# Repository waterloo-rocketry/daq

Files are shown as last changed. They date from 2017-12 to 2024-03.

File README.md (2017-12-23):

# Waterloo Rocketry Data Acquisition System

Work in progress repo for the next iteration of the WR DAQ. This revision focuses on modularity and extensibility, with the ability to easily add more sensors as required. Schematics of the last revision are in `old/`. The new system supports the following:
* Strain gauges
* 12V pressure transducers
* thermistors/RTDs based on need
* SD card logging using an Arduino
* Logging to an NI DAQ instrumentation module

The system is broken up into boards based on sensor type, with each board managing its own power requirements without the need for a central power board. Sensors can be added by populating more boards (and designing new ones to be added on if necessary). `docs/` will be populated as the project progresses.

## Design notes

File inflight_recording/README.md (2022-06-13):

# HOW TO SETUP IN-FLIGHT RECORDING USING A RASPBERRY PI ZERO W

## Instructions

### Basic Pi setup

1. Flash a default copy of the Raspbian OS onto a large-capacity SD card (pereferably 128 GB or larger)
1. [Enable SSH](https://www.raspberrypi.org/documentation/remote-access/ssh/README.md) (skip to step 3 - `Enable SSH on a headless Raspberry Pi`)
1. Follow the `Direct USB Connection (Pi Zero / Zero W Only)` section of [this article](https://www.tomshardware.com/reviews/raspberry-pi-headless-setup-how-to,6028.html)
1. Plug the camera module into the Pi using a ribbon cable
1. Use a USB Micro B cable to connect the Pi to a computer (ensure you are connecting to the 'USB' port, not the 'PWR' port)
1. SSH into the Pi (using PuTTY, or similar):
    1. host/ip: raspberrypi.local if USB connected OR the IP of the Pi (see [Getting the IP of the Pi](#getting-the-ip-of-the-pi) for help)
    1. user: pi
    1. password: raspberry
    1. port: 22
1. Inside the ssh session, [enable the camera](https://www.raspberrypi.org/documentation/configuration/camera.md) and [connect the Pi to the Internet](https://www.raspberrypi.org/documentation/configuration/wireless/wireless-cli.md)
1. Update the [Raspbian OS](https://www.raspberrypi.org/documentation/raspbian/updating.md) (Internet connection required)

### Setting up the picam

1. Establish an FTP connection (or however you want to transfer files) to the Pi (see [Transferring files to and from the Pi](#transferring-files-to-and-from-the-pi) for help)
1. In the `home/Documents` folder, make a folder called `picam`
1. Download all files in this directory onto your computer (do not transfer them yet)
1. **Convert ALL line endings in the `.sh` and `.service` files to UNIX-style line endings (LF)**
    1. Skipping this step will result in the service NOT running.
    1. In Notepad++, this can be done by opening the file -> edit -> EOL conversion -> UNIX (LF)
1. Transfer the converted files into `picam` on the raspberry pi (see [Transferring files to and from the Pi](#transferring-files-to-and-from-the-pi) for help)
1. SSH into the Pi
1. Run `cd picam` to move into the correct directory
1. Run `chmod u+x picam_setup.sh`
1. Run `./picam_setup.sh` to configure the picam service

Done! Next time the Pi restarts, the camera will run and will stream its data over the network.

### Streaming footage

1. Download [mpv](https://mpv.io/), a media player (does not require installation, it's a portable software)
1. Extract the contents of the zip to a file, and open a command prompt to that location
1. Ensure the Pi is turned on, and give it a minute to start up fully
1. Run `mpv.exe --no-cache --untimed --no-demuxer-thread udp://<IPv4 Address of Your PC>:<PORT>` (see [Getting the IP of your PC](#getting-the-ip-of-your-pc) for help)
    1. The port and IP are the ones you specified in `picam_setup.sh`. If you don't know it, you'll have to check what is currently on the Pi.

Done! The stream should appear. If there is significant delay, try restarting the stream. Generally, about ~1 second of delay is expected. If no footage appears, check your firewall settings and ensure the port(s) allow UDP traffic.

## Additional Info

### Getting the IP of the Pi

1. If you are able to connect to the Pi via USB:
    1. SSH into the Pi (see [Basic Pi setup](#basic-pi-setup))
    1. Run `ifconfig`
    1. Under `wlan0`, the copy and record the address next to `inet` (usually something like 192.168.x.xx)
1. If you do not have access to the Pi:
    1. Login to your WiFi network's remote gateway (this is usually only possible if you are the administrator of your wifi network)
    1. Find the active devices list
    1. Copy the IP Address of the Raspberry Pi on the network.

If you do not have physical access AND you are not the administrator of the WiFi network, there is no way to get this address unfortunately.

### Getting the IP of your PC

These are Windows instructions. If you have Linux, you already know how to do this. If you have a mac, MPV doesn't work on it anyway.

1. Ensure you are connected to the same network as the Pi
1. Open a command prompt
1. Run `ipconfig`
1. Scroll to `Wireless LAN adapter Wi-Fi` (if you're on ethernet, it'll be `Ethernet adapter Ethernet`)
1. Find your `IPv4` address. This is your local IP.

Similar to above in [Getting the IP of the Pi](#getting-the-ip-of-the-pi), if you have access to the network's remote gateway, you can find your PC in the active devices list (works on any device)

### Transferring files to and from the Pi

There are many ways to accomplish this but an easy, free way to do this is using FileZilla, an FTP client.

1. Download and install [FileZilla](https://filezilla-project.org/)
1. Input the following details in the top-bar to establish a connection to the Pi
    1. host/ip: raspberrypi.local if USB connected OR the IP of the Pi (see [Getting the IP of the Pi](#getting-the-ip-of-the-pi) for help)
    1. user: pi
    1. password: raspberry
    1. port: 22
1. Click `quickconnect`
1. The `/home/pi` folder should appear in the `remote site` tab
1. PiCam files are stored in the `picam` directory.
1. To upload files, simply navigate to the folder containing the desired file(s) on the `local site`, select them, right click -> upload
1. To download files, simply navigate to the folder containing the desired file(s) on the `remote site`, select them, right click -> download

### Tips if you're running into issues

If lagging occurs, it may be possible that the `gpu_mem` component of `/boot/config.txt` needs to be upped to 256. We upped it on the prototype, but did not test if it was required

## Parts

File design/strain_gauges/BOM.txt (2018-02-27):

Strain Gauge Board BOM

Part Name, Digikey Number
LT-1460, LT1460GIZ-10#PBF-ND
TL780-15, 296-14326-5-ND
INA126, INA126PA-ND
2 Pin Conn, 609-4725-ND
3 Pin Conn, 277-1722-ND
4 Pin Conn, 277-1860-ND

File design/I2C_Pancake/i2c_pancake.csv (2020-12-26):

Source: | C:\Users\zacha\Desktop\Zachary\Rocketry\daq\daq\design\I2C Pancake\i2c_pancake.sch
Date: | 30-Sep-2020 16:33:39
Tool: | Eeschema (5.1.4)-1
Generator: | C:\Program Files\KiCad\bin\scripting\plugins/bom_csv_grouped_by_value.py
Component Count: | 39
Individual Components:
Item | Qty | Reference(s) | Value | LibPart | Footprint | Datasheet
 |  | C1 | 0.1 uF | Device:C | footprints:C_0805_HandSoldering | ~
 |  | C2 | 10 uF | Device:C | footprints:C_0805_HandSoldering | ~
 |  | C3 | 0.1uF | Device:C | footprints:C_0805_HandSoldering | ~
 |  | C4 | 0.1uF | i2c_pancake-rescue:C-device-i2c_pancake-rescue | footprints:C_0805_HandSoldering
 |  | C5 | 0.1uF | i2c_pancake-rescue:C-device-i2c_pancake-rescue | footprints:C_0805_HandSoldering
 |  | C6 | 0.1uF | i2c_pancake-rescue:C-device-i2c_pancake-rescue | footprints:C_0805_HandSoldering
 |  | D1 | LED | Device:LED | LED_SMD:LED_1206_3216Metric_Pad1.42x1.75mm_HandSolder | ~
 |  | D2 | DDZ4V7ASF-7 | Device:D_Zener_ALT | Diode_SMD:D_SOD-323F | ~
 |  | D3 | DDZ4V7ASF-7 | Device:D_Zener_ALT | Diode_SMD:D_SOD-323F | ~
 |  | D4 | DDZ4V7ASF-7 | Device:D_Zener_ALT | Diode_SMD:D_SOD-323F | ~
 |  | F1 | Fuse | i2c_pancake-rescue:Fuse-device-i2c_pancake-rescue | Fuse:Fuse_0805_2012Metric_Pad1.15x1.40mm_HandSolder
 |  | J1 | Conn_01x05_Male | Connector:Conn_01x05_Male | Connector_JST:JST_XH_S5B-XH-A-1_1x05_P2.50mm_Horizontal | ~
 |  | J2 | Conn_01x05_Male | Connector:Conn_01x05_Male | Connector_JST:JST_XH_S5B-XH-A-1_1x05_P2.50mm_Horizontal | ~
 |  | J3 | Conn_01x03 | i2c_pancake-rescue:Conn_01x03-strain_gauges_rtr-rescue-i2c_pancake-rescue | TerminalBlock_Phoenix:TerminalBlock_Phoenix_MKDS-1,5-3_1x03_P5.00mm_Horizontal
 |  | J4 | Conn_01x03 | i2c_pancake-rescue:Conn_01x03-strain_gauges_rtr-rescue-i2c_pancake-rescue | TerminalBlock_Phoenix:TerminalBlock_Phoenix_MKDS-1,5-3_1x03_P5.00mm_Horizontal
 |  | J5 | Conn_01x05_Female | Connector:Conn_01x05_Female | footprints:PinHeader_5x2.54_SMD_90deg_952-3198-1-ND | ~
 |  | J6 | Conn_01x04 | i2c_pancake-rescue:Conn_01x04-strain_gauges_rtr-rescue-i2c_pancake-rescue | TerminalBlock_Phoenix:TerminalBlock_Phoenix_MKDS-1,5-4_1x04_P5.00mm_Horizontal
 |  | J7 | Conn_01x04 | i2c_pancake-rescue:Conn_01x04-strain_gauges_rtr-rescue-i2c_pancake-rescue | TerminalBlock_Phoenix:TerminalBlock_Phoenix_MKDS-1,5-4_1x04_P5.00mm_Horizontal
 |  | J8 | Conn_01x04 | i2c_pancake-rescue:Conn_01x04-strain_gauges_rtr-rescue-i2c_pancake-rescue | TerminalBlock_Phoenix:TerminalBlock_Phoenix_MKDS-1,5-4_1x04_P5.00mm_Horizontal
 |  | R1 | 10K | Device:R | footprints:R_0805_HandSoldering | ~
 |  | R2 | 10K | i2c_pancake-rescue:R-device-i2c_pancake-rescue | footprints:R_0805_HandSoldering
 |  | R3 | 5K | i2c_pancake-rescue:R-device-i2c_pancake-rescue | footprints:R_0805_HandSoldering
 |  | R4 | 330 | Device:R | footprints:R_0805_HandSoldering | ~
 |  | R5 | 10K | Device:R | footprints:R_0805_HandSoldering | ~
 |  | R6 | 10K | Device:R | footprints:R_0805_HandSoldering | ~
 |  | R7 | 10K | Device:R | footprints:R_0805_HandSoldering | ~
 |  | R8 | 10K | Device:R | footprints:R_0805_HandSoldering | ~
 |  | R9 | R | i2c_pancake-rescue:R-device-i2c_pancake-rescue | footprints:R_0805_HandSoldering
 |  | R10 | 0 | i2c_pancake-rescue:R-device-i2c_pancake-rescue | footprints:R_0805_HandSoldering
 |  | R11 | R | i2c_pancake-rescue:R-device-i2c_pancake-rescue | footprints:R_0805_HandSoldering
 |  | R12 | 0 | i2c_pancake-rescue:R-device-i2c_pancake-rescue | footprints:R_0805_HandSoldering
 |  | R13 | R | i2c_pancake-rescue:R-device-i2c_pancake-rescue | footprints:R_0805_HandSoldering
 |  | R14 | 0 | i2c_pancake-rescue:R-device-i2c_pancake-rescue | footprints:R_0805_HandSoldering
 |  | SW1 | SW_DIP_x04 | Switch:SW_DIP_x04 | footprints:DIP_SWITCH_4X2 | ~
 |  | U1 | TL750M10CKVU | tlv750m10:TL750M05CKVURG3 | footprints:TL750M10CKVU | http://www.ti.com/lit/ds/symlink/tl750m.pdf?ts=1588185394744
 |  | U2 | PIC16F1826-ISO | i2c_pancake-rescue:PIC16F1826-ISO-rlcsv3_modular-rescue | custom:PIC16F1826-ISO
 |  | U3 | INA826 | i2c_pancake-rescue:INA826-daq_components-i2c_pancake-rescue | footprints:SOIC-8_3.9x4.9mm_Pitch1.27mm_HandSoldering
 |  | U4 | INA826 | i2c_pancake-rescue:INA826-daq_components-i2c_pancake-rescue | footprints:SOIC-8_3.9x4.9mm_Pitch1.27mm_HandSoldering
 |  | U5 | INA826 | i2c_pancake-rescue:INA826-daq_components-i2c_pancake-rescue | footprints:SOIC-8_3.9x4.9mm_Pitch1.27mm_HandSoldering
Collated Components:
Item | Qty | Reference(s) | Value | LibPart | Footprint | Datasheet
1 | 1 | C1 | 0.1 uF | Device:C | footprints:C_0805_HandSoldering | ~
2 | 1 | C2 | 10 uF | Device:C | footprints:C_0805_HandSoldering | ~
3 | 1 | C3 | 0.1uF | Device:C | footprints:C_0805_HandSoldering | ~
4 | 3 | C4, C5, C6 | 0.1uF | i2c_pancake-rescue:C-device-i2c_pancake-rescue | footprints:C_0805_HandSoldering
5 | 1 | D1 | LED | Device:LED | LED_SMD:LED_1206_3216Metric_Pad1.42x1.75mm_HandSolder | ~
6 | 3 | D2, D3, D4 | DDZ4V7ASF-7 | Device:D_Zener_ALT | Diode_SMD:D_SOD-323F | ~
7 | 1 | F1 | Fuse | i2c_pancake-rescue:Fuse-device-i2c_pancake-rescue | Fuse:Fuse_0805_2012Metric_Pad1.15x1.40mm_HandSolder
8 | 2 | J1, J2 | Conn_01x05_Male | Connector:Conn_01x05_Male | Connector_JST:JST_XH_S5B-XH-A-1_1x05_P2.50mm_Horizontal | ~
9 | 2 | J3, J4 | Conn_01x03 | i2c_pancake-rescue:Conn_01x03-strain_gauges_rtr-rescue-i2c_pancake-rescue | TerminalBlock_Phoenix:TerminalBlock_Phoenix_MKDS-1,5-3_1x03_P5.00mm_Horizontal
10 | 1 | J5 | Conn_01x05_Female | Connector:Conn_01x05_Female | footprints:PinHeader_5x2.54_SMD_90deg_952-3198-1-ND | ~
11 | 3 | J6, J7, J8 | Conn_01x04 | i2c_pancake-rescue:Conn_01x04-strain_gauges_rtr-rescue-i2c_pancake-rescue | TerminalBlock_Phoenix:TerminalBlock_Phoenix_MKDS-1,5-4_1x04_P5.00mm_Horizontal
12 | 5 | R1, R5, R6, R7, R8 | 10K | Device:R | footprints:R_0805_HandSoldering | ~
13 | 1 | R2 | 10K | i2c_pancake-rescue:R-device-i2c_pancake-rescue | footprints:R_0805_HandSoldering
14 | 1 | R3 | 5K | i2c_pancake-rescue:R-device-i2c_pancake-rescue | footprints:R_0805_HandSoldering
15 | 1 | R4 | 330 | Device:R | footprints:R_0805_HandSoldering | ~
16 | 3 | R9, R11, R13 | R | i2c_pancake-rescue:R-device-i2c_pancake-rescue | footprints:R_0805_HandSoldering
17 | 3 | R10, R12, R14 | 0 | i2c_pancake-rescue:R-device-i2c_pancake-rescue | footprints:R_0805_HandSoldering
18 | 1 | SW1 | SW_DIP_x04 | Switch:SW_DIP_x04 | footprints:DIP_SWITCH_4X2 | ~
19 | 1 | U1 | TL750M10CKVU | tlv750m10:TL750M05CKVURG3 | footprints:TL750M10CKVU | http://www.ti.com/lit/ds/symlink/tl750m.pdf?ts=1588185394744
20 | 1 | U2 | PIC16F1826-ISO | i2c_pancake-rescue:PIC16F1826-ISO-rlcsv3_modular-rescue | custom:PIC16F1826-ISO
21 | 3 | U3, U4, U5 | INA826 | i2c_pancake-rescue:INA826-daq_components-i2c_pancake-rescue | footprints:SOIC-8_3.9x4.9mm_Pitch1.27mm_HandSoldering

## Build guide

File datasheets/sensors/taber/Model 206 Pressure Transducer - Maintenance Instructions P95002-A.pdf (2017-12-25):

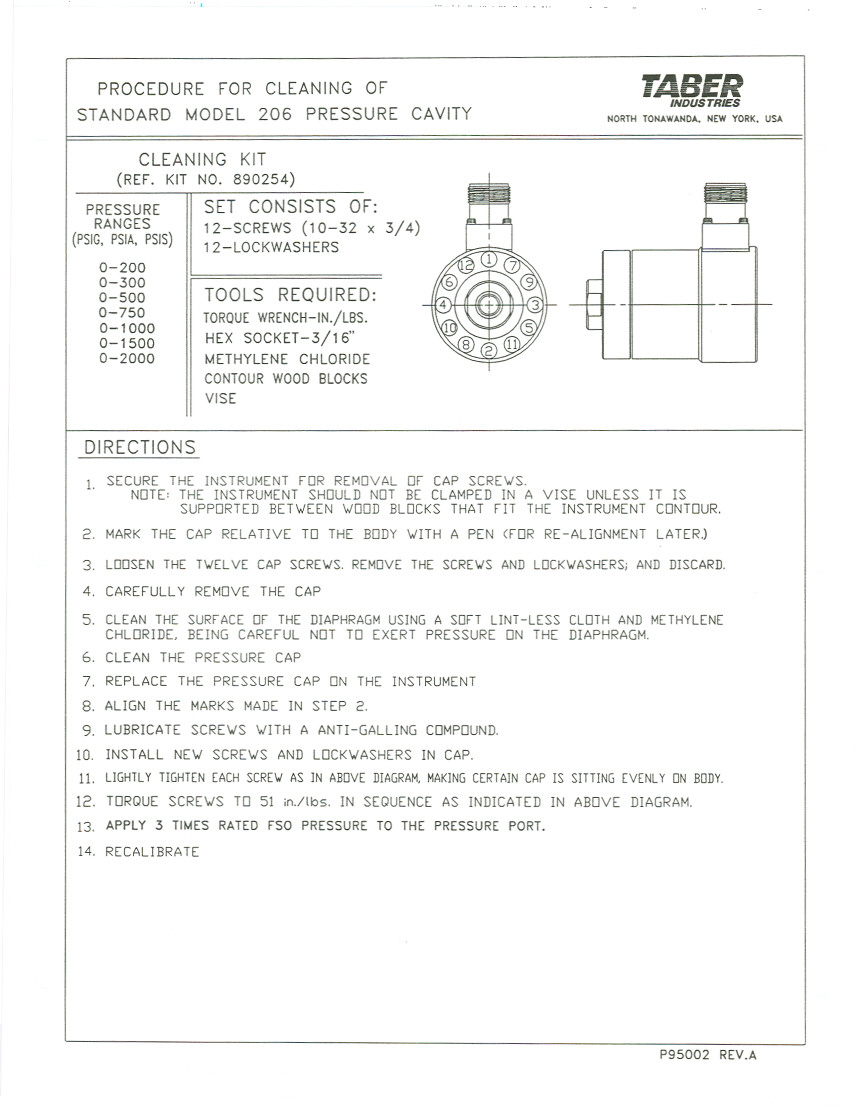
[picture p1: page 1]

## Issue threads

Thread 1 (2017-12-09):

Temperature measurement boards

amihaila, 2017-12-09:
Either thermistors or RTDs, depending on use case. Thermistors are enough if we don't want to measure any high temperatures.

Closed 2020-10-06.

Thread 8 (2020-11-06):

Schematic for Strain gauge rtr is out of date

ewdyang, 2020-11-06:
The 15V regulator in the schematics has been changed to a 12V version (TL780-12KCS)

BluCodeGH, 2022-11-04:
Closing as no longer relevant

Closed 2022-11-04.

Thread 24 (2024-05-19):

Thermocouple board issues

JasonBrave, 2024-05-19:
1. Screw terminals are not labeled

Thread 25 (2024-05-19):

Patch Panel Board Issue

JasonBrave, 2024-05-19:
12 pin terminal is in wrong direction

Pdada1, 2024-05-21:
Silkscreen Issues
-No silkscreen on power jumpers (unknown which pin is which voltage)
-Same with the big terminal block (weidmuller)

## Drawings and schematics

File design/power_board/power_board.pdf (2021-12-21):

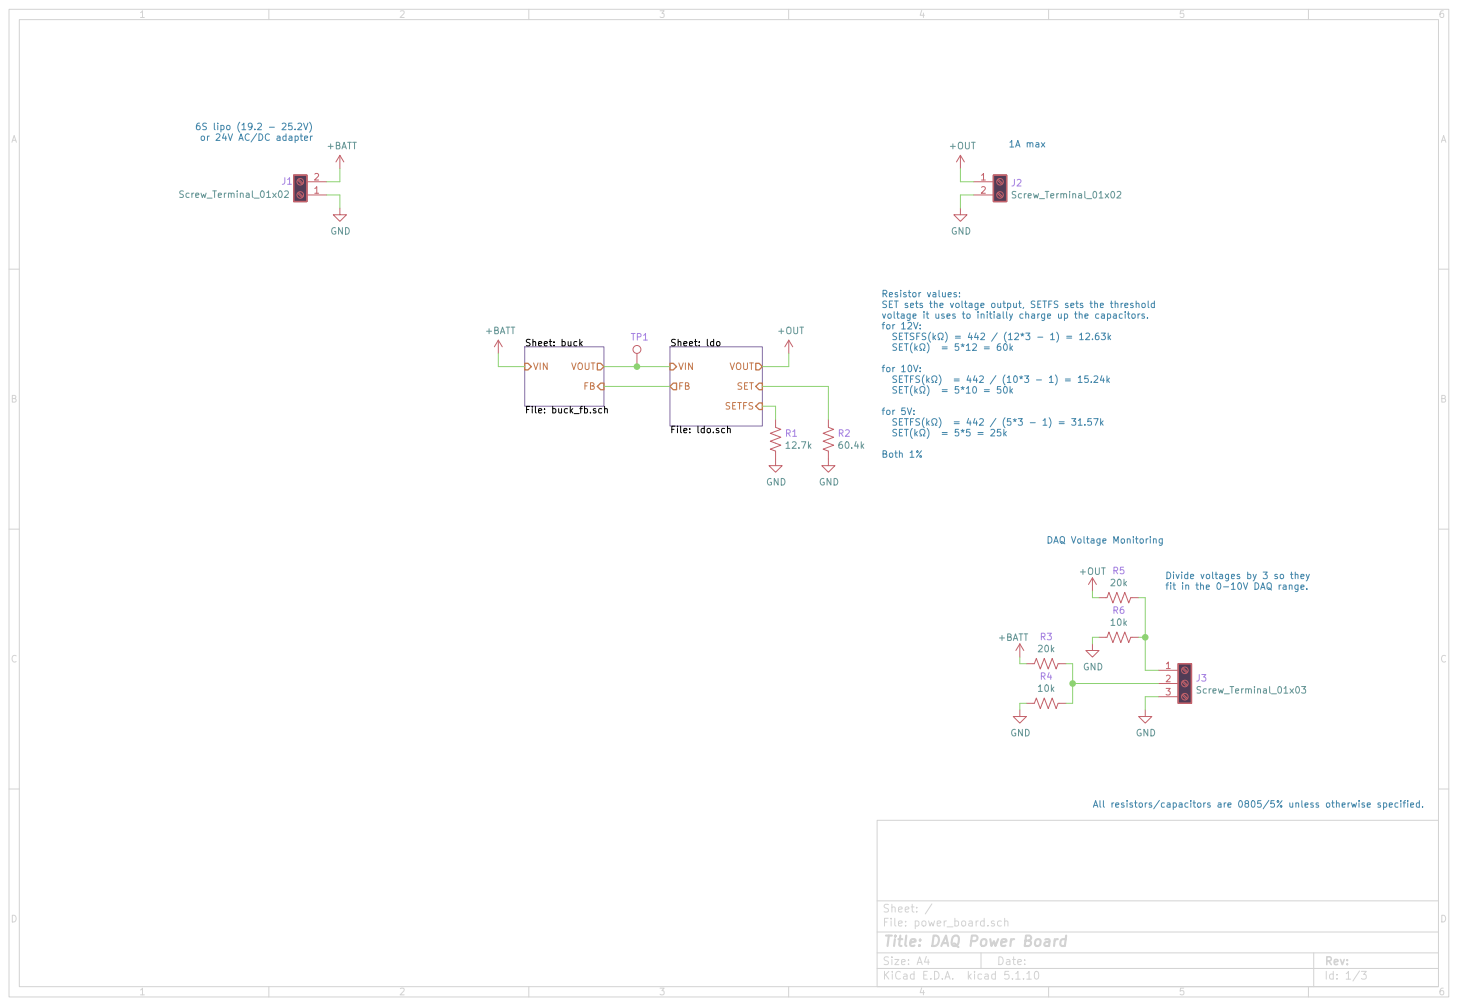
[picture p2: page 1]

6S lipo (19.2 - 25.2V)
or 24V AC/DC adapter

DAQ Voltage Monitoring Resistor values: SET sets the voltage output, SETFS sets the threshold

voltage it uses to initially charge up the capacitors.
for 12V:
SETSFS(k) = 442 / (12*3 - 1) = 12.63k
SET(k) = 5*12 = 60k

Sheet: ldo File: ldo.sch VIN

Divide voltages by 3 so they
fit in the 0-10V DAQ range.

All resistors/capacitors are 0805/5% unless otherwise specified.

File: power_board.sch Sheet: /
Id: 1/3 Title: DAQ Power Board

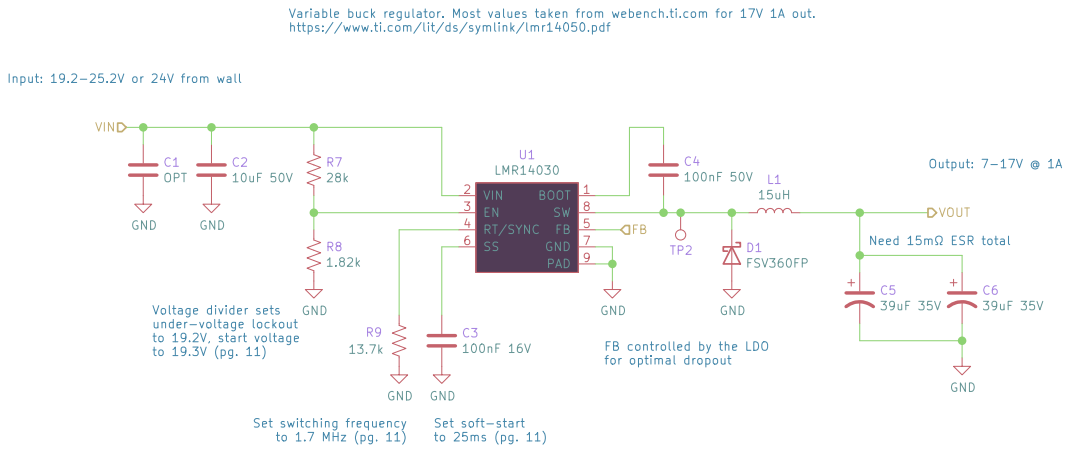
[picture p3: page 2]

Variable buck regulator. Most values taken from webench.ti.com for 17V 1A out.
https://www.ti.com/lit/ds/symlink/lmr14050.pdf

Input: 19.2-25.2V or 24V from wall

Output: 7-17V @ 1A Need 15m ESR total Voltage divider sets

for optimal dropout Set soft-start

FB controlled by the LDO

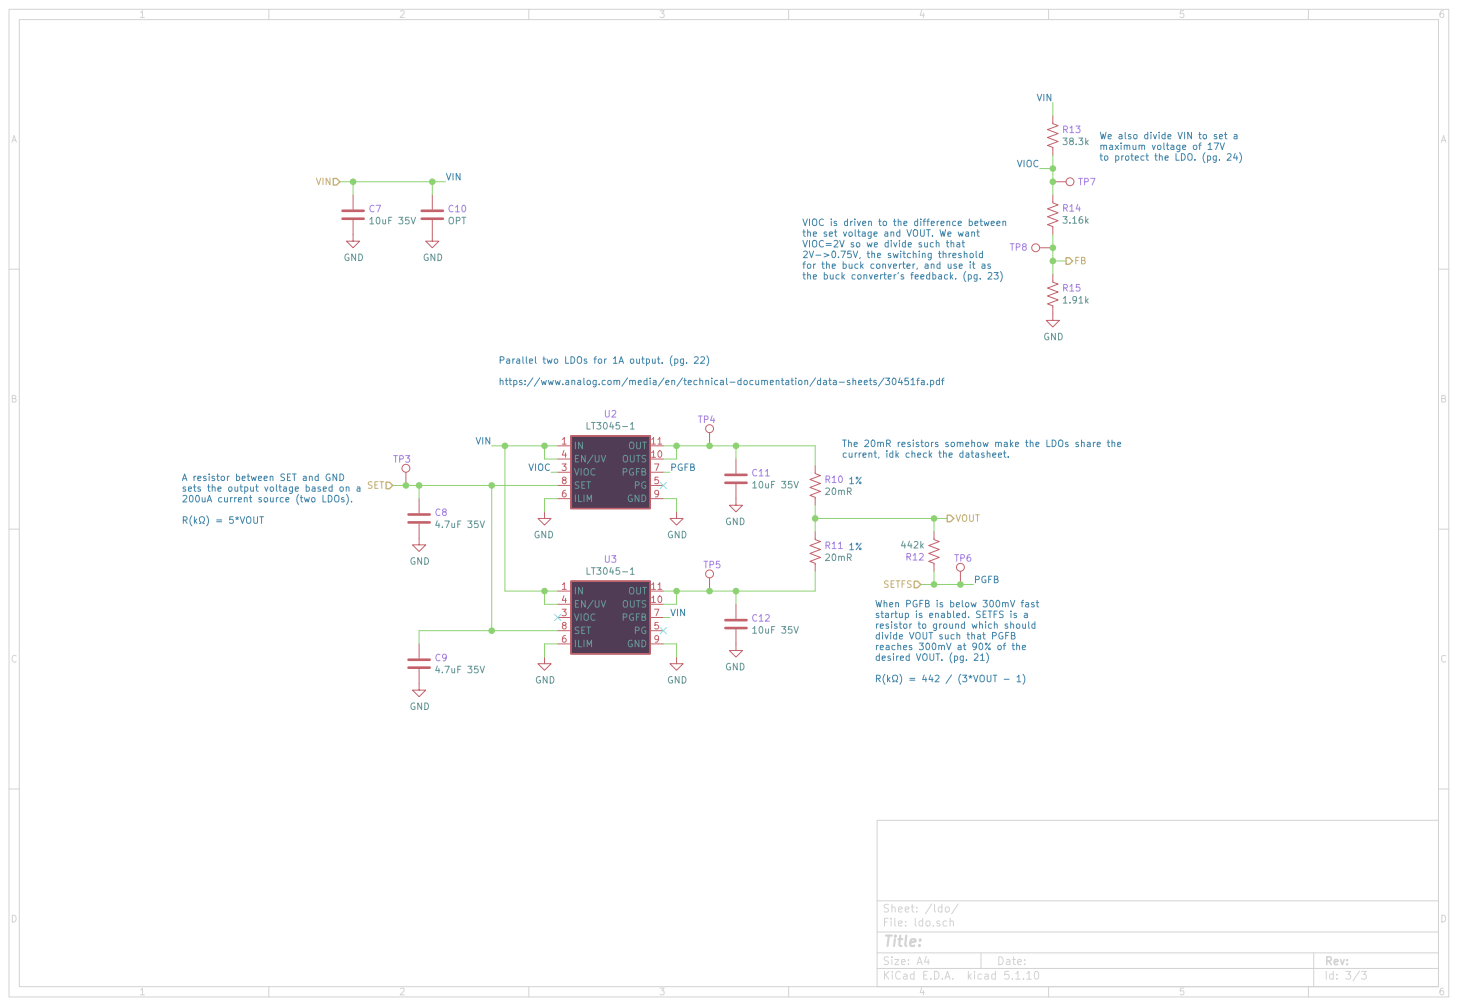
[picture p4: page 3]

to protect the LDO. (pg. 24) 1%

VIOC is driven to the difference between
the set voltage and VOUT. We want VIOC=2V so we divide such that 2V->0.75V, the switching threshold

for the buck converter, and use it as

current, idk check the datasheet. Parallel two LDOs for 1A output. (pg. 22)

https://www.analog.com/media/en/technical-documentation/data-sheets/30451fa.pdf A resistor between SET and GND

The 20mR resistors somehow make the LDOs share the

sets the output voltage based on a
200uA current source (two LDOs).

resistor to ground which should
divide VOUT such that PGFB
reaches 300mV at 90% of the
desired VOUT. (pg. 21)

Id: 3/3 Title: File: ldo.sch Sheet: /ldo/

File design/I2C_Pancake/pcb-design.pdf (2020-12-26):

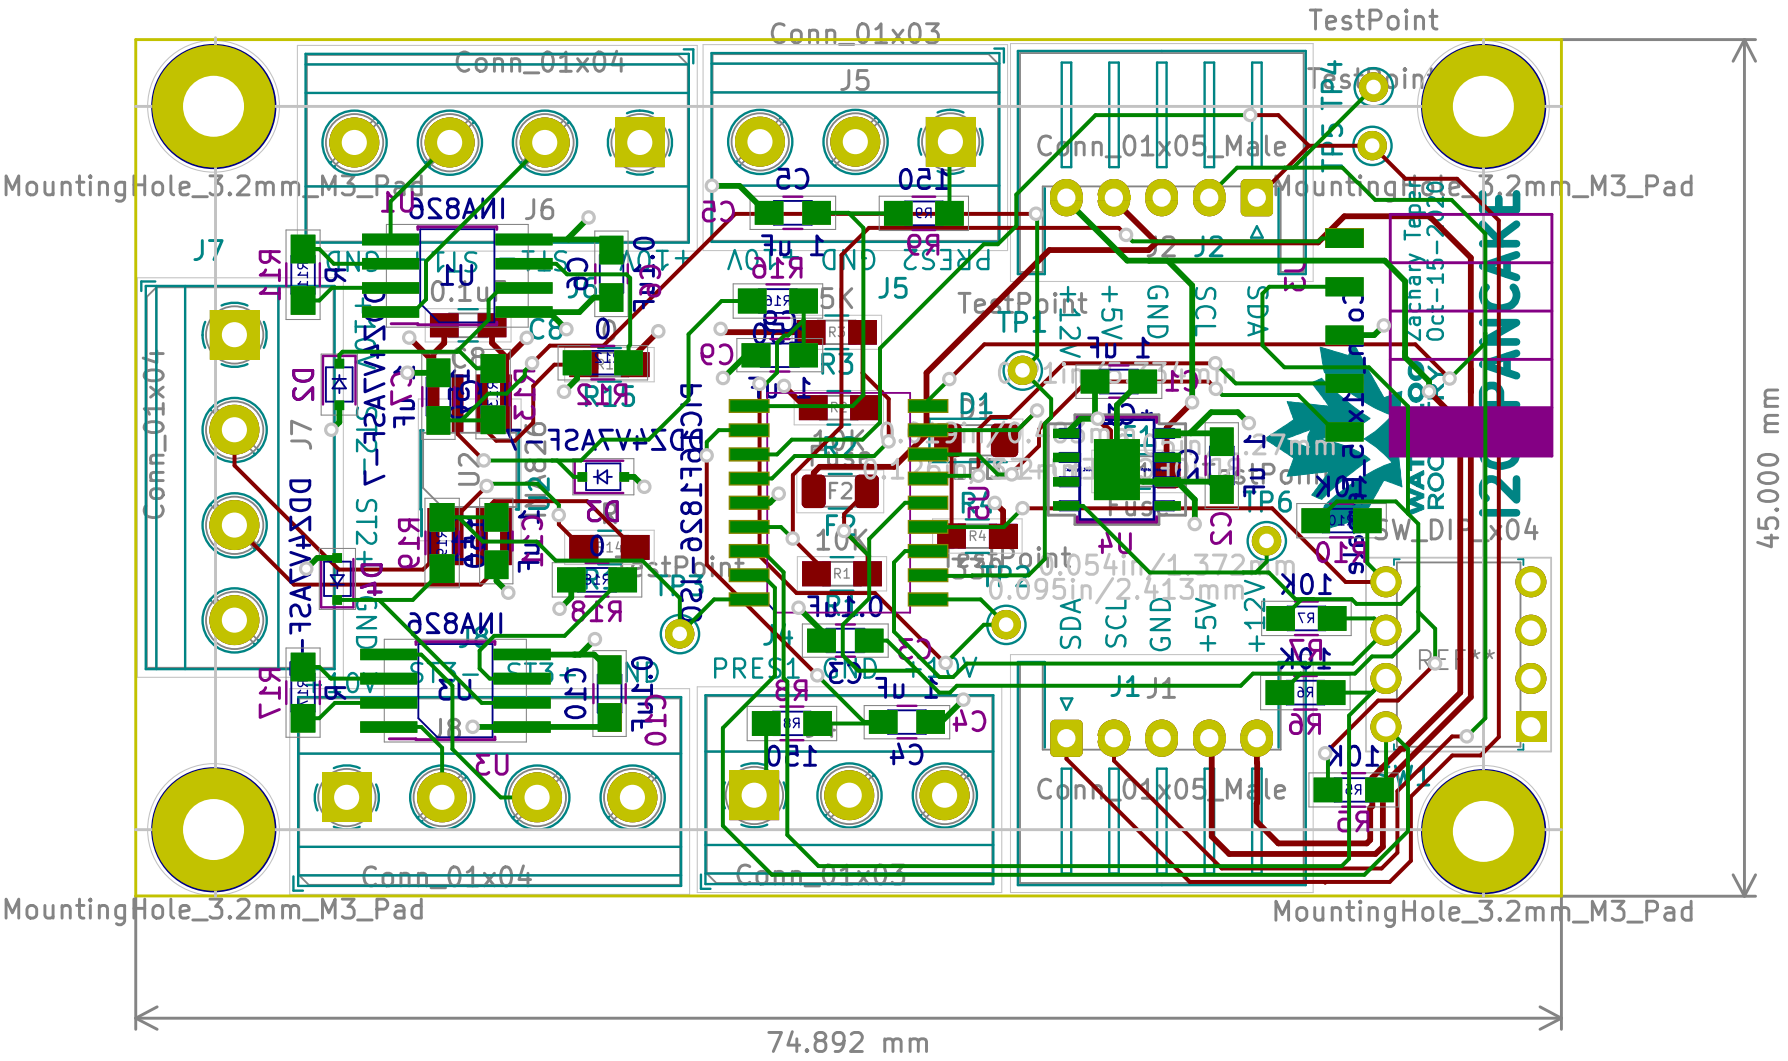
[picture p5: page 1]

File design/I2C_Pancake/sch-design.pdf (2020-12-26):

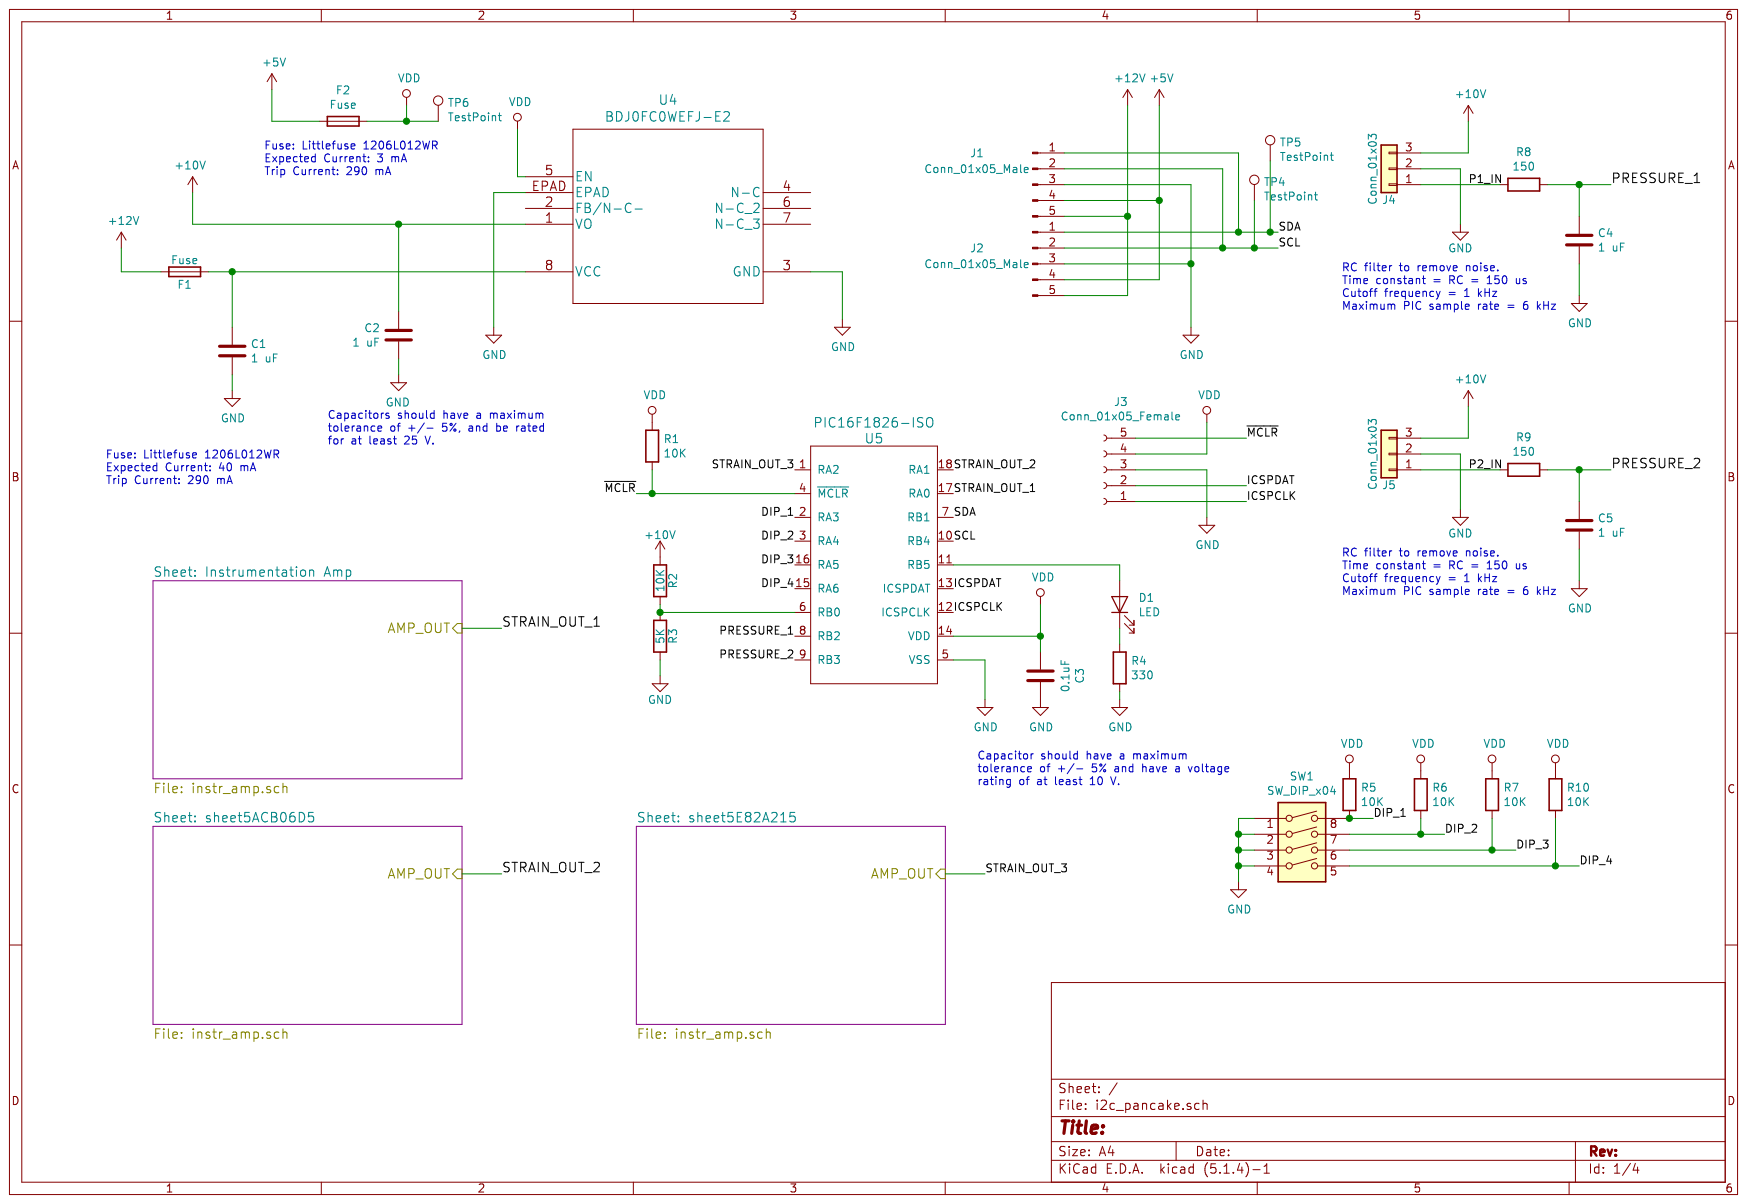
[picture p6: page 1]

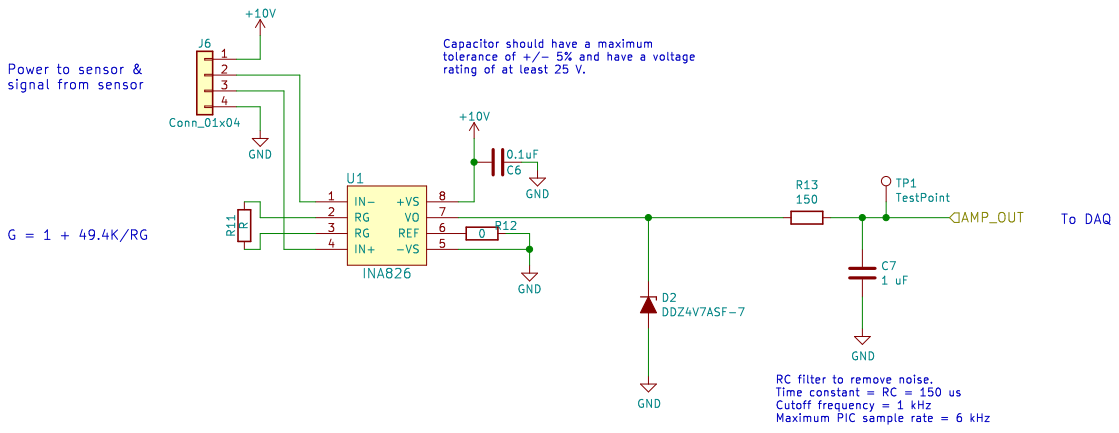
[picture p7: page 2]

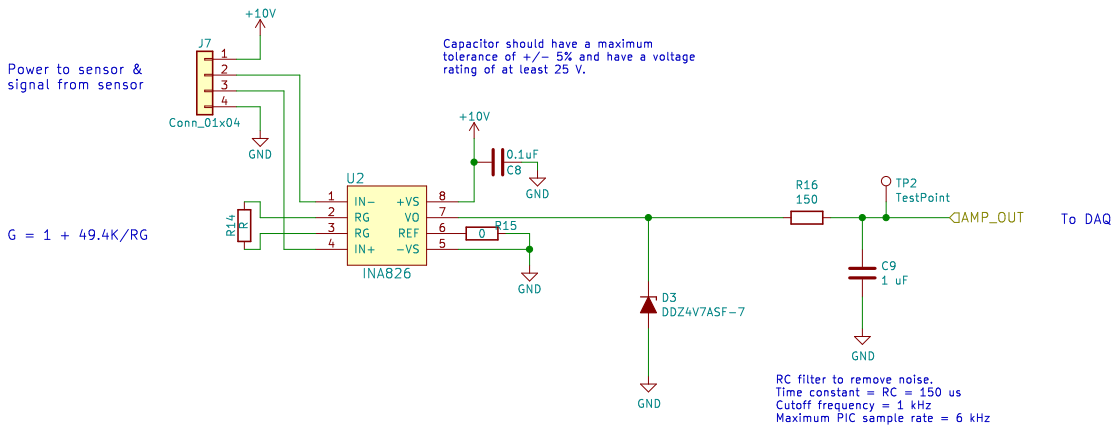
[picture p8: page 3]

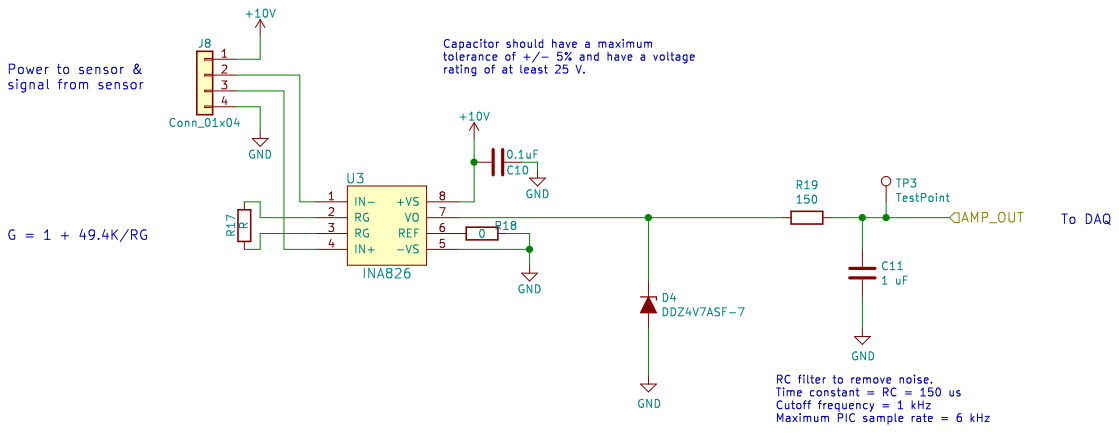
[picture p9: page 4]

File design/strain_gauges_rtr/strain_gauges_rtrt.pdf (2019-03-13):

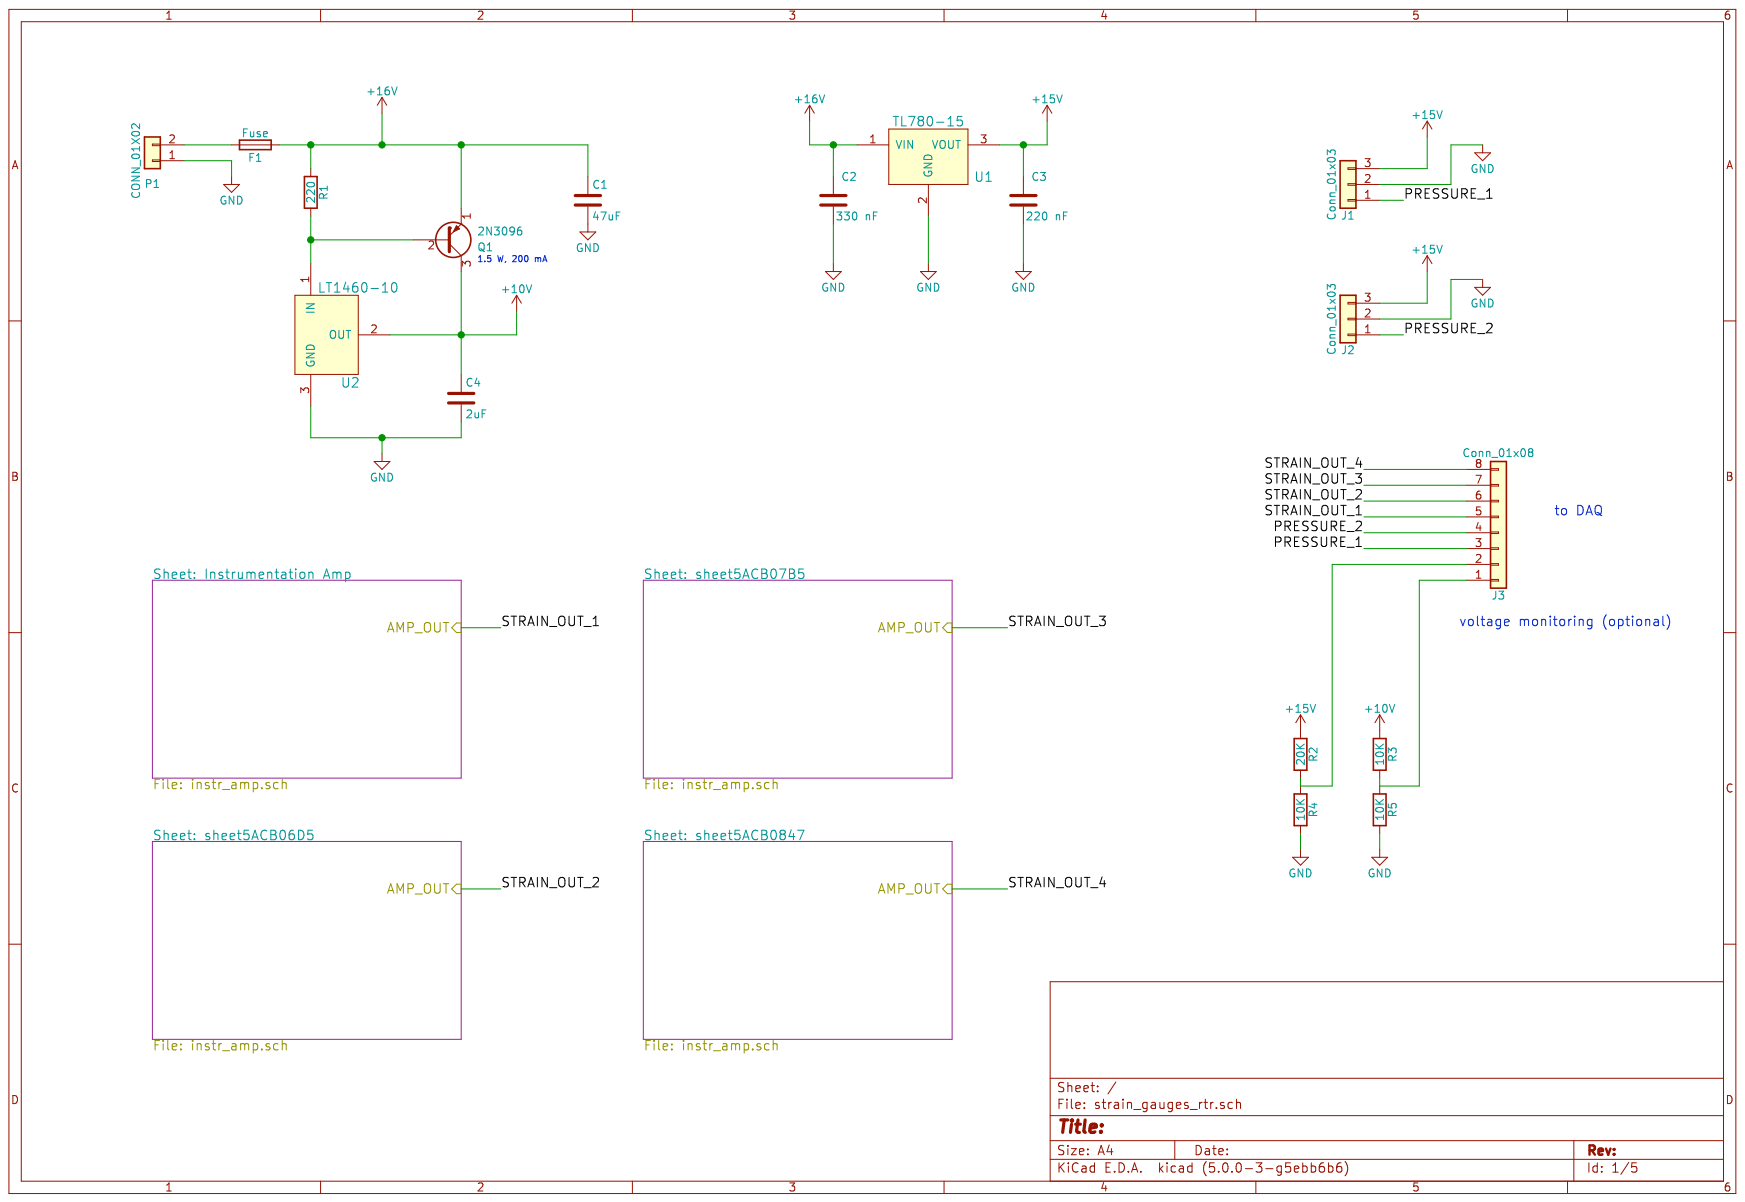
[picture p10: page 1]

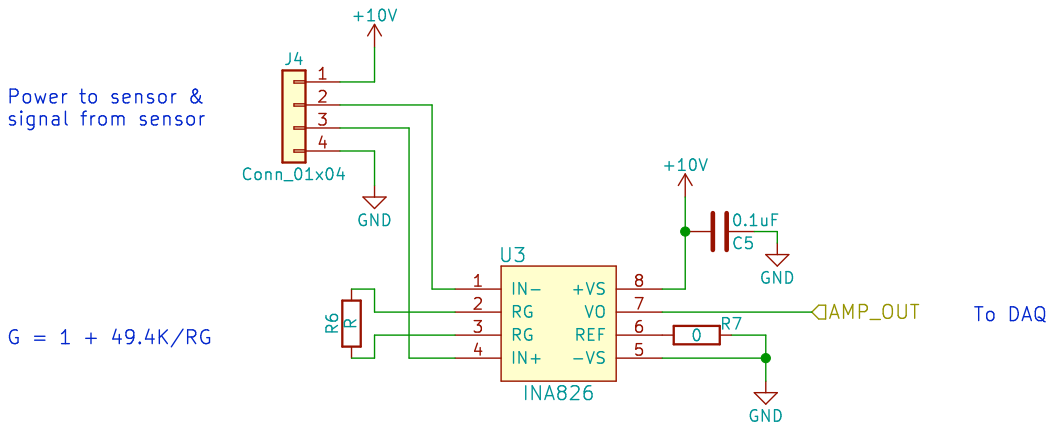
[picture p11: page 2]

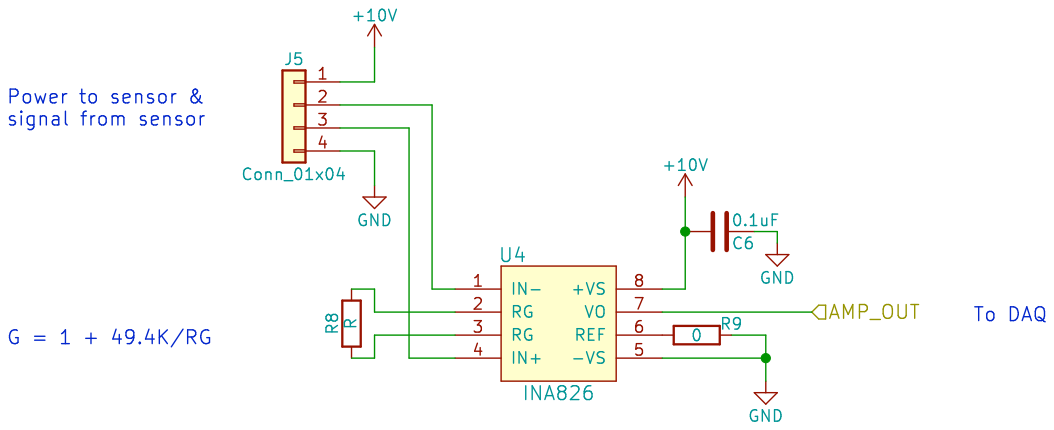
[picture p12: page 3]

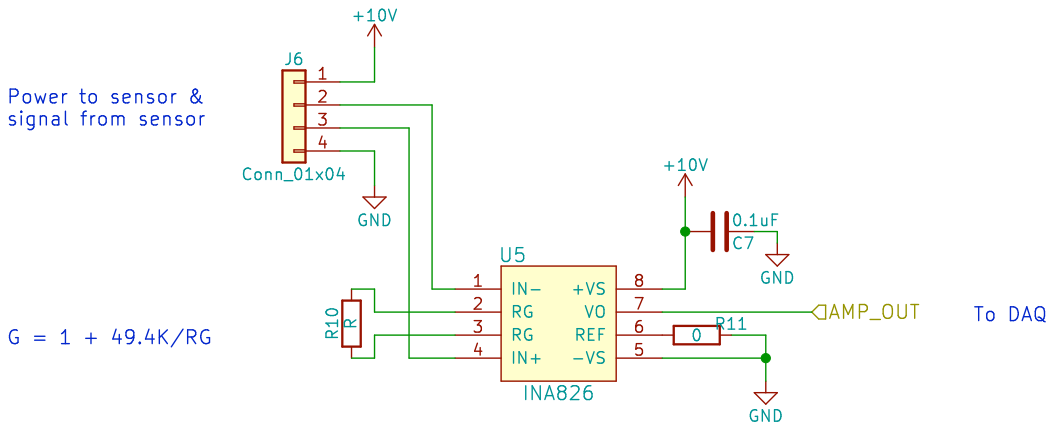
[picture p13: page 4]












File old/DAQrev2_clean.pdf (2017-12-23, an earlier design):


Load Cell Amplified GND
+12V GND

2 P6 Sensor Power GND Note: All 3 strain gauge sensors are

on the PCB. 1 P8SP2 amplified

powered off the same precision voltage
reference, even though the outputs go

which means the op amp responsible for
maintaining the reference is running in open
loop. This reference shouldn't be used. Not
sure why it's connected to a screw terminal

2 P?SS Pressure Sensor Power GND
For documentation only. 1

TODO in next rev. Add decoupling caps
on amplifier power inputs.

DAQ Rev2 Schematic (cleaned up)





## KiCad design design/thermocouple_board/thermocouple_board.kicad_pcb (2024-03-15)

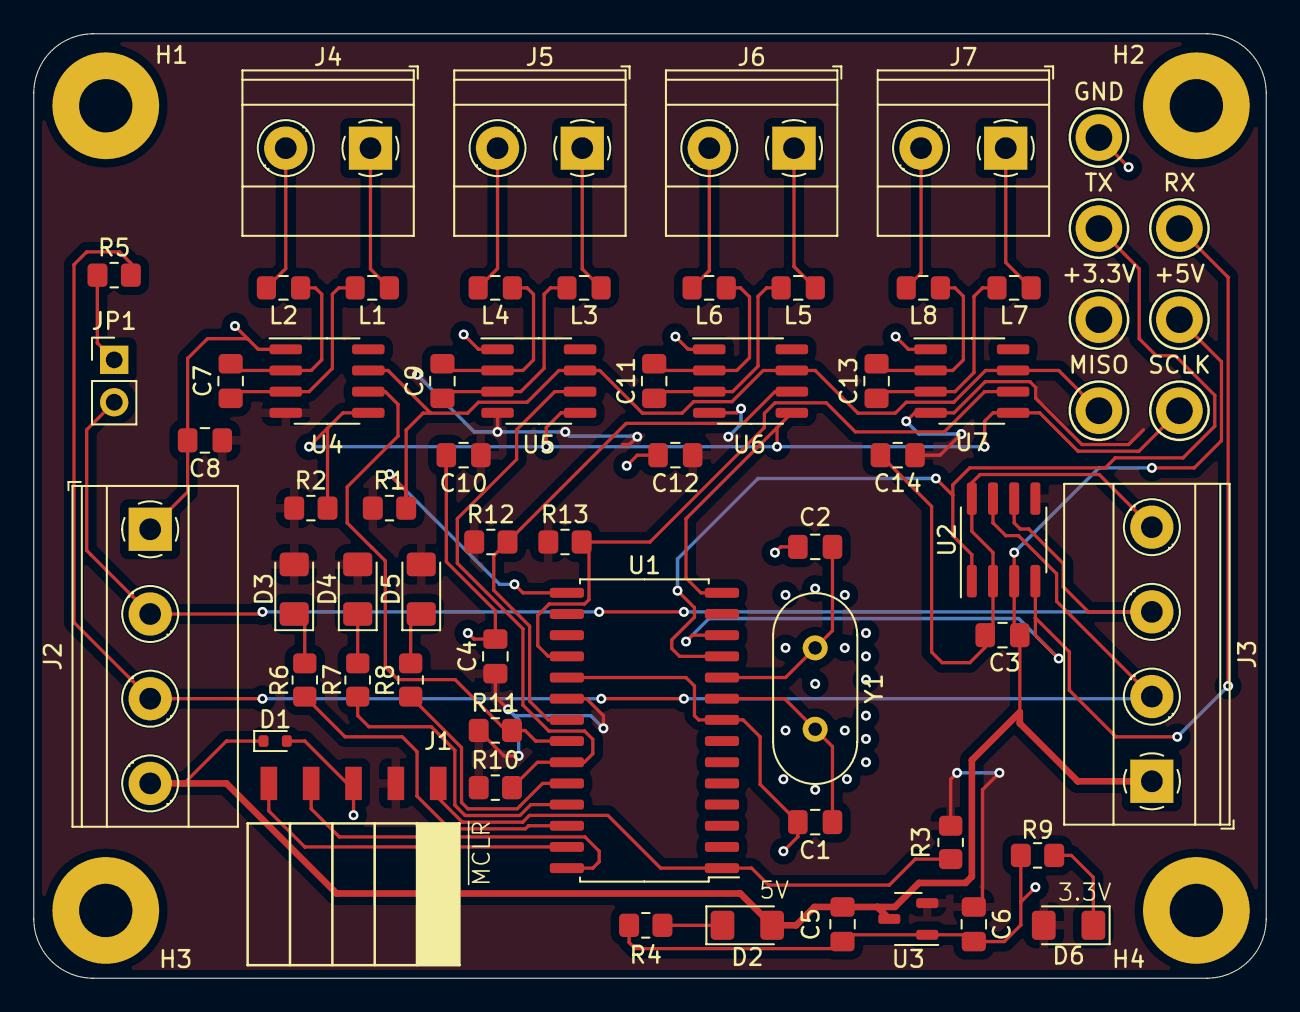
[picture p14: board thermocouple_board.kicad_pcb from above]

Board: 2 copper layers, 73.9 x 56.6 mm, 68 parts (0 on the bottom side), 43 nets.

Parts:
+3.3V, +5V: TestPoint; TestPoint_Keystone_5005-5009_Compact
C1, C2: 27pF; C_0805_2012Metric_Pad1.18x1.45mm_HandSolder
C3: 10uF; C_0805_2012Metric_Pad1.18x1.45mm_HandSolder
C4, C7, C8, C9, C10, C11, C12, C13, C14: 0.1uF; C_0805_2012Metric_Pad1.18x1.45mm_HandSolder
C5: 4.7uF; C_0805_2012Metric_Pad1.18x1.45mm_HandSolder
C6: 22uF; C_0805_2012Metric_Pad1.18x1.45mm_HandSolder
D1: 1.5KExxA; D_SOD-523
D2, D6: GREEN; LED_1206_3216Metric_Pad1.42x1.75mm_HandSolder
D3: YELLOW; LED_1206_3216Metric_Pad1.42x1.75mm_HandSolder
D4: ORANGE; LED_1206_3216Metric_Pad1.42x1.75mm_HandSolder
D5: RED; LED_1206_3216Metric_Pad1.42x1.75mm_HandSolder
GND: TestPoint; TestPoint_Keystone_5005-5009_Compact
H1, H2, H3, H4: MountingHole; MountingHole_3.2mm_M3_Pad
J1: Prog Conn; PinHeader_5x2.54_SMD_90deg_952-3198-1-ND
J2: CAN Conn; TerminalBlock_Phoenix_MKDS-1,5-4-5.08_1x04_P5.08mm_Horizont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
J3: CAN Ext Conn; TerminalBlock_Phoenix_MKDS-1,5-4-5.08_1x04_P5.08mm_Horizont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
J4, J5, J6, J7: Thermocouple conn; TerminalBlock_Phoenix_MKDS-1,5-2-5.08_1x02_P5.08mm_Horizont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
JP1: Jumper; PinHeader_1x02_P2.54mm_Vertical
L1, L2, L3, L4, L5, L6, L7, L8: 1K @ 100 MHz; Fuse_0805_2012Metric_Pad1.15x1.40mm_HandSolder
MISO: TestPoint; TestPoint_Keystone_5005-5009_Compact
R1, R2, R3, R10, R11, R12, R13: 10k; R_0805_2012Metric_Pad1.20x1.40mm_HandSolder
R4: 220R; R_0805_2012Metric_Pad1.20x1.40mm_HandSolder
R5, R6, R7, R8, R9: 120R; R_0805_2012Metric_Pad1.20x1.40mm_HandSolder
RX: TestPoint; TestPoint_Keystone_5005-5009_Compact
SCLK: TestPoint; TestPoint_Keystone_5005-5009_Compact
TX: TestPoint; TestPoint_Keystone_5005-5009_Compact
U1: PIC18LF26K83; SOIC-28W_7.5x17.9mm_P1.27mm
U2: MCP2562; SOIC-8_3.9x4.9mm_P1.27mm
U3: AP2120N-3.3TRG1; SOT-23-3
U4, U5, U6, U7: MAX31855KASA; SOIC-8_3.9x4.9mm_P1.27mm
Y1: 12 MHz; Crystal_HC49-4H_Vertical

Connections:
+3.3V: +3.3V.1, C4.1, C6.1, C8.1, C10.1, C12.1, C14.1, D3.2 (A), D4.2 (A), D5.2 (A), D6.2 (A), J1.2, R1.1, R2.1, R3.1, R10.1, R11.1, R12.1, R13.1, U1.20 (VDD), U2.5 (VIO), U3.2 (VO), U4.4 (VCC), U5.4 (VCC), U6.4 (VCC), U7.4 (VCC)
+5V: +5V.1, C3.1, C5.1, D1.1 (A1), D2.2 (A), J2.4, J3.1, U2.3 (VDD), U3.3 (VI)
/CANH: J2.3, J3.2, R5.2, U2.7 (CANH)
/CANL: J2.2, J3.3, JP1.2 (B), U2.6 (CANL)
/CAN_RX: RX.1, U1.12 (RC1), U2.4 (RXD)
/CAN_TX: TX.1, U1.11 (RC0), U2.1 (TXD)
/CS1: R10.2, U1.23 (RB2), U5.6 (~CS)
/CS2: R11.2, U1.22 (RB1), U4.6 (~CS)
/CS3: R12.2, U1.21 (RB0), U6.6 (~CS)
/CS4: R13.2, U1.18 (RC7), U7.6 (~CS)
/ICSPCLK: J1.5, U1.27 (RB6/ICSPCLK)
/ICSPDAT: J1.4, U1.28 (RB7/ICSPDAT)
/OSC1: C1.1, U1.9 (RA7/OSC1), Y1.2
/OSC2: C2.1, U1.10 (RA6/OSC2), Y1.1
/~MCLR: J1.1, R3.2, U1.1 (~MCLR)
GND: C1.2, C2.2, C3.2, C4.2, C5.2, C6.2, C8.2, C10.2, C12.2, C14.2, D1.2 (A2), GND.1, J1.3, J2.1, J3.4, R4.2, R9.2, U1.8 (VSS), U1.19 (VSS), U2.2 (VSS), U2.8 (STBY), U3.1 (GND), U4.1 (GND), U5.1 (GND), U6.1 (GND), U7.1 (GND)
MISO: MISO.1, R1.2, U1.15 (RC4), U4.7 (SDO), U5.7 (SDO), U6.7 (SDO), U7.7 (SDO)
unnamed: D2.1 (K), R4.1
unnamed: D3.1 (K), R6.1
unnamed: D4.1 (K), R7.1
unnamed: D5.1 (K), R8.1
unnamed: D6.1 (K), R9.1
unnamed: J4.1, L1.1
unnamed: J4.2, L2.1
unnamed: J5.1, L3.1
unnamed: J5.2, L4.1
unnamed: J6.1, L5.1
unnamed: J6.2, L6.1
unnamed: J7.1, L7.1
unnamed: J7.2, L8.1
unnamed: JP1.1 (A), R5.1
unnamed: R8.2, U1.24 (RB3)
unnamed: R7.2, U1.25 (RB4)
unnamed: R6.2, U1.26 (RB5)
unnamed: C7.1, L1.2, U4.3 (T+)
unnamed: C7.2, L2.2, U4.2 (T-)
unnamed: C9.1, L3.2, U5.3 (T+)
unnamed: C9.2, L4.2, U5.2 (T-)
unnamed: C11.1, L5.2, U6.3 (T+)
unnamed: C11.2, L6.2, U6.2 (T-)
unnamed: C13.1, L7.2, U7.3 (T+)
unnamed: C13.2, L8.2, U7.2 (T-)
SCLK: R2.2, SCLK.1, U1.14 (RC3), U4.5 (SCK), U5.5 (SCK), U6.5 (SCK), U7.5 (SCK)

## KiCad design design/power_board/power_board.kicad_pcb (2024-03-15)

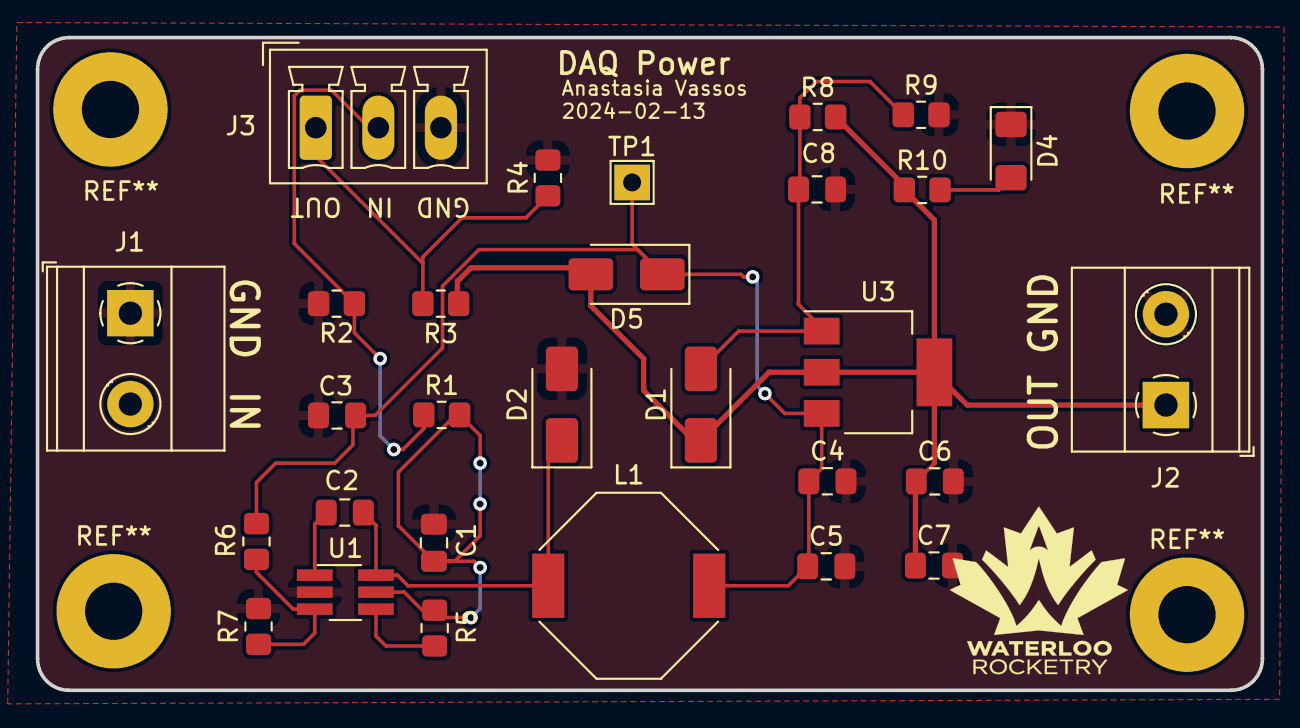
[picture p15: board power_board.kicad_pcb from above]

Board: 2 copper layers, 68.5 x 36.5 mm, 29 parts (0 on the bottom side), 12 nets.

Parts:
C1, C4, C6, C8: 10uF; C_0805_2012Metric_Pad1.18x1.45mm_HandSolder
C2, C7: 1uF; C_0805_2012Metric_Pad1.18x1.45mm_HandSolder
C3: 20uF; C_0805_2012Metric_Pad1.18x1.45mm_HandSolder
C5: 0.1uF; C_0805_2012Metric_Pad1.18x1.45mm_HandSolder
D1, D5: US1A; D_SMA
D2: B130-E3/5AT; D_SMA
D4: LED; D_1206_3216Metric_Pad1.42x1.75mm_HandSolder
J1, J2: Screw_Terminal_01x02; TerminalBlock_Phoenix_MKDS-1,5-2-5.08_1x02_P5.08mm_Horizont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
J3: Screw_Terminal_01x03; PhoenixContact_MCV_1,5_3-G-3.5_1x03_P3.50mm_Vertical
L1: 22uH; L_Bourns-SRU1028_10.0x10.0mm
R1, R3: 20k; R_0805_2012Metric_Pad1.20x1.40mm_HandSolder
R2, R4, R7: 10k; R_0805_2012Metric_Pad1.20x1.40mm_HandSolder
R5: 100k; R_0805_2012Metric_Pad1.20x1.40mm_HandSolder
R6: 277.58k; R_0805_2012Metric_Pad1.20x1.40mm_HandSolder
R8: 240R; R_0805_2012Metric_Pad1.20x1.40mm_HandSolder
R9, R10: _k; R_0805_2012Metric_Pad1.20x1.40mm_HandSolder
TP1: TestPoint; TestPoint_THTPad_2.0x2.0mm_Drill1.0mm
U1: LV2862YDDCR; TSOT-23-6_HandSoldering
U3: LM317MDCYR; SOT-223-3_TabPin2

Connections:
+BATT: C1.1, J1.2, R1.2, R5.1, U1.5 (VIN)
+OUT: C6.1, C7.1, D1.1 (K), D5.2 (A), J2.1, R3.2, R8.2, R10.1, U3.2 (VO)
/buck/VOUT: C3.1, C4.1, C5.1, D5.1 (K), L1.2, R6.1, TP1.1, U3.3 (VI)
GND: C1.2, C3.2, C4.2, C5.2, C6.2, C7.2, C8.1, D2.2 (A), D4.1 (K), J1.1, J2.2, J3.3, R2.2, R4.2, R7.2, R9.2, U1.2 (GND)
unnamed: C8.2, D1.2 (A), R8.1, R9.1, U3.1 (ADJ)
unnamed: C2.1, D2.1 (K), L1.1, U1.6 (SW)
unnamed: D4.2 (A), R10.2
unnamed: J3.1, R3.1, R4.1
unnamed: J3.2, R1.1, R2.1
unnamed: C2.2, U1.1 (CB)
unnamed: R6.2, R7.1, U1.3 (FB)
unnamed: R5.2, U1.4 (SHDN_N)

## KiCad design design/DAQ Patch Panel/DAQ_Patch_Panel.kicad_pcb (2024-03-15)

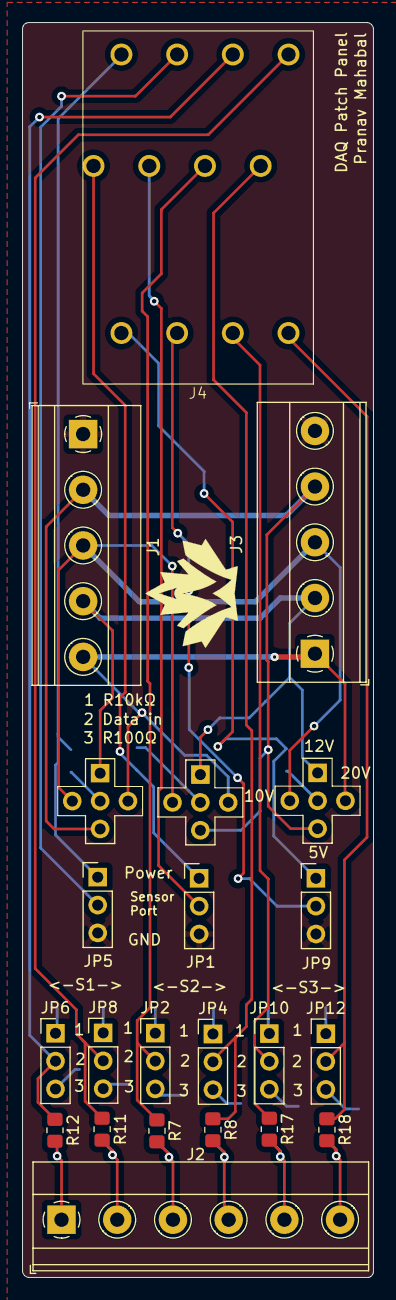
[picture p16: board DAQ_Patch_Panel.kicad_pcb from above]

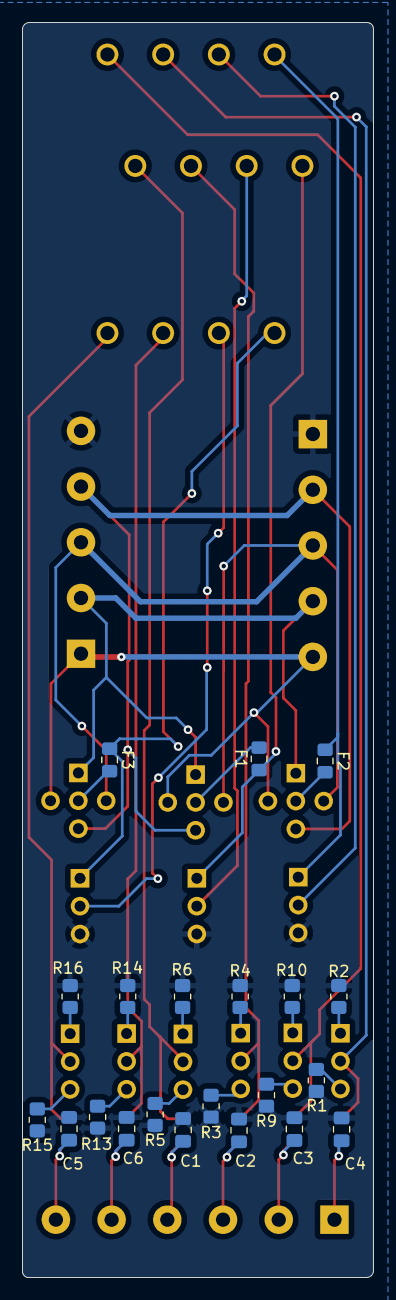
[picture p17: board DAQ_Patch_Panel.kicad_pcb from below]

Board: 2 copper layers, 32.0 x 114.4 mm, 43 parts (21 on the bottom side), 38 nets.

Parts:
C1, C2, C3, C4, C5, C6: 80nF; C_0805_2012Metric_Pad1.18x1.45mm_HandSolder
F1, F2, F3: 50mA; Fuse_0805_2012Metric_Pad1.15x1.40mm_HandSolder
J1: Power Terminal 1; TerminalBlock_Phoenix_MKDS-1,5-5-5.08_1x05_P5.08mm_Horizont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
J2: Data Output Terminal; TerminalBlock_Phoenix_MKDS-1,5-6-5.08_1x06_P5.08mm_Horizont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
J3: Power Terminal 2; TerminalBlock_Phoenix_MKDS-1,5-5-5.08_1x05_P5.08mm_Horizont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
J4: Weidmuller LM3RZF
JP1, JP5, JP9: GND OR POWER; PinHeader_1x03_P2.54mm_Vertical
JP2, JP6, JP10: RESISTOR JUMPER 2; PinHeader_1x03_P2.54mm_Vertical
JP3, JP7, JP11: Power_Jumpers; 4-Way-Jumper
JP4, JP8, JP12: RESISTOR JUMPER 1; PinHeader_1x03_P2.54mm_Vertical
R1, R3, R5, R9, R13, R15: 100R 1%; R_0805_2012Metric_Pad1.20x1.40mm_HandSolder
R2, R4, R6, R10, R14, R16: 10k 1%; R_0805_2012Metric_Pad1.20x1.40mm_HandSolder
R7, R8, R11, R12, R17, R18: 100R; R_0805_2012Metric_Pad1.20x1.40mm_HandSolder

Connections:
+5V: J1.2, J3.4, JP3.3 (B), JP7.3 (B), JP11.3 (B)
+10V: J1.3, J3.3, JP3.4 (C), JP7.4 (C), JP11.4 (C)
+12V: J1.4, J3.2, JP3.1 (A), JP7.1 (A), JP11.1 (A)
+20V: J1.5, J3.1, JP3.5 (C), JP7.5 (C), JP11.5 (C)
/S1DATA1: C4.1, J2.1, R12.2
/S1DATA2: C3.1, J2.2, R11.2
/S1GND: J4.2, JP5.2 (C)
/S1IN1: J4.3, JP6.2 (C), R12.1
/S1IN2: J4.4, JP8.2 (C), R11.1
/S1POWER: F2.1, J4.1, JP5.1 (A)
/S2DATA1: C2.1, J2.3, R7.2
/S2DATA2: C1.1, J2.4, R8.2
/S2GND: J4.6, JP1.2 (C)
/S2IN1: J4.7, JP2.2 (C), R7.1
/S2IN2: J4.8, JP4.2 (C), R8.1
/S2POWER: F1.1, J4.5, JP1.1 (A)
/S3DATA1: C6.1, J2.5, R17.2
/S3DATA2: C5.1, J2.6, R18.2
/S3GND: J4.10, JP9.2 (C)
/S3IN1: J4.11, JP10.2 (C), R17.1
/S3IN2: J4.12, JP12.2 (C), R18.1
/S3POWER: F3.1, J4.9, JP9.1 (A)
GND: C1.2, C2.2, C3.2, C4.2, C5.2, C6.2, J1.1, J3.5, JP1.3 (B), JP5.3 (B), JP9.3 (B), R1.2, R2.2, R3.2, R4.2, R5.2, R6.2, R9.2, R10.2, R13.2, R14.2, R15.2, R16.2
unnamed: F1.2, JP3.2 (C)
unnamed: F2.2, JP7.2 (C)
unnamed: F3.2, JP11.2 (C)
unnamed: JP2.1 (A), R4.1
unnamed: JP2.3 (B), R3.1
unnamed: JP4.1 (A), R6.1
unnamed: JP4.3 (B), R5.1
unnamed: JP6.1 (A), R2.1
unnamed: JP6.3 (B), R1.1
unnamed: JP8.1 (A), R10.1
unnamed: JP8.3 (B), R9.1
unnamed: JP10.1 (A), R14.1
unnamed: JP10.3 (B), R13.1
unnamed: JP12.1 (A), R16.1
unnamed: JP12.3 (B), R15.1

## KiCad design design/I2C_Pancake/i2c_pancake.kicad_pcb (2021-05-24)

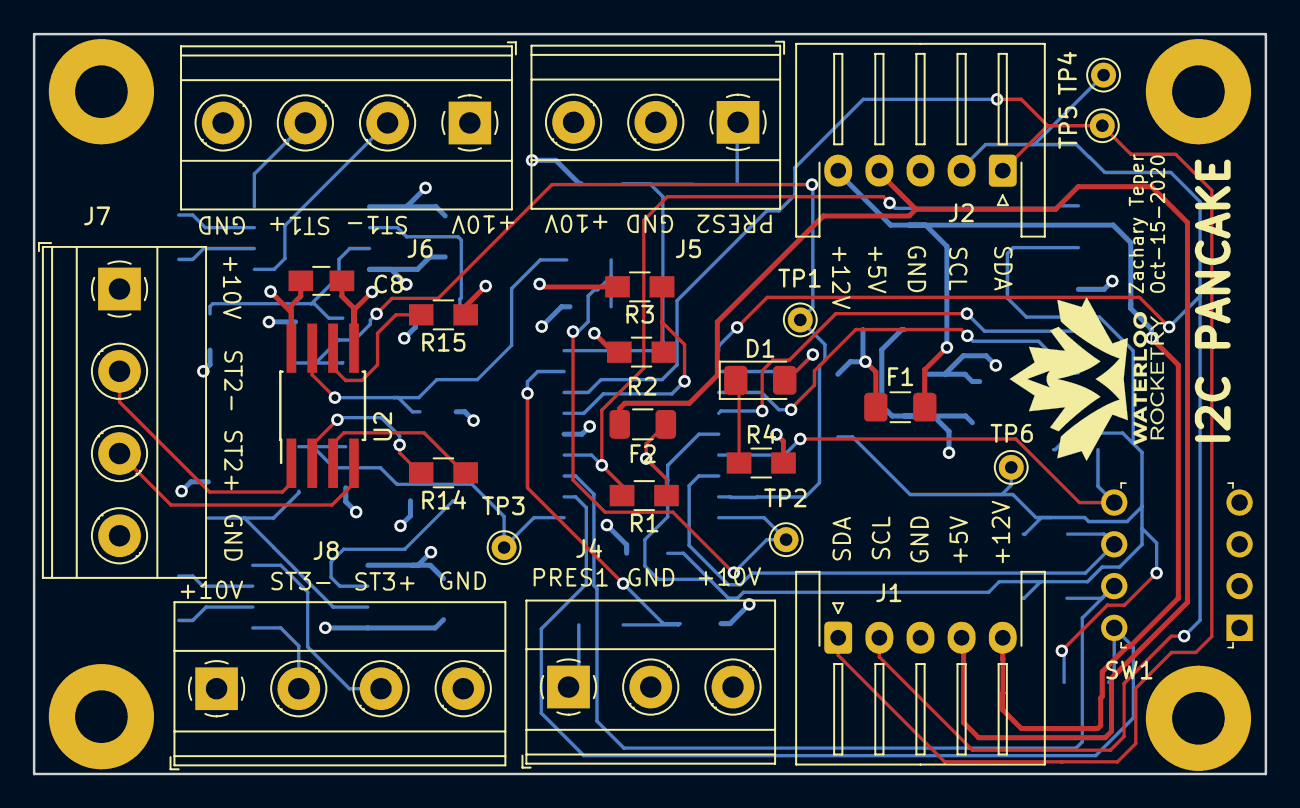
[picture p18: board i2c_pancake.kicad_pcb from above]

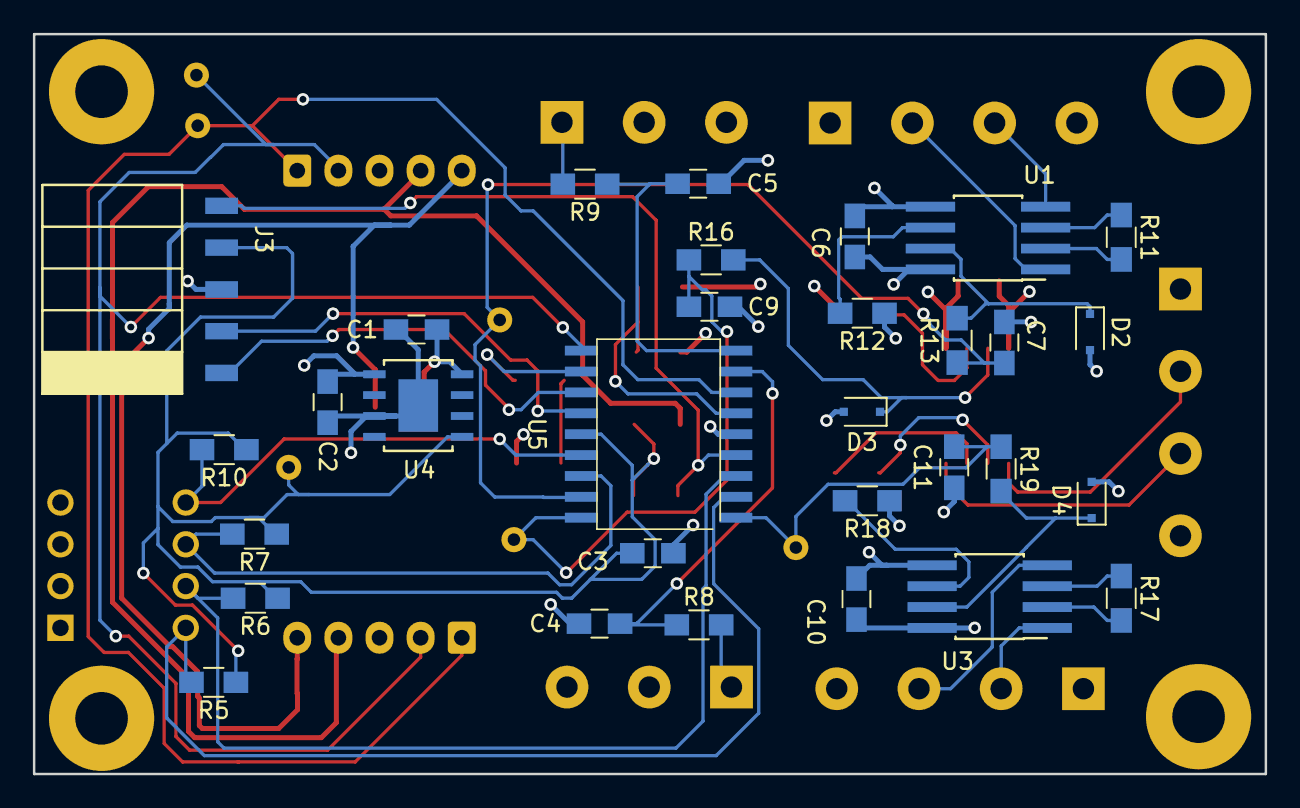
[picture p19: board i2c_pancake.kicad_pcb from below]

Board: 4 copper layers, 74.9 x 45.0 mm, 56 parts (31 on the bottom side), 43 nets.

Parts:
C1, C2, C4, C5, C7, C9, C11: 1 uF; C_0805_HandSoldering
C3, C6, C8, C10: 0.1uF; C_0805_HandSoldering
D1: LED; LED_1206_3216Metric_Pad1.42x1.75mm_HandSolder
D2, D3, D4: DDZ4V7ASF-7; D_SOD-323F
F1: Fuse; Fuse_1206_3216Metric_Pad1.42x1.75mm_HandSolder
F2: Fuse; Fuse_1206_3216Metric
J1, J2: Conn_01x05_Male; JST_XH_S5B-XH-A-1_1x05_P2.50mm_Horizontal
J3: Conn_01x05_Female; PinHeader_5x2.54_SMD_90deg_952-3198-1-ND
J4, J5: Conn_01x03; TerminalBlock_Phoenix_MKDS-1,5-3_1x03_P5.00mm_Horizontal
J6, J7, J8: Conn_01x04; TerminalBlock_Phoenix_MKDS-1,5-4_1x04_P5.00mm_Horizontal
R1, R2, R5, R6, R7, R10: 10K; R_0805_HandSoldering
R3: 5K; R_0805_HandSoldering
R4: 330; R_0805_HandSoldering
R8, R9, R13, R16, R19: 150; R_0805_HandSoldering
R11, R14, R17: R; R_0805_HandSoldering
R12, R15, R18: 0; R_0805_HandSoldering
SW1: SW_DIP_x04; DIP_SWITCH_4X2
TP1, TP2, TP3, TP4, TP5, TP6: TestPoint
U1, U2, U3: INA826; SOIC-8_3.9x4.9mm_Pitch1.27mm_HandSoldering
U4: BDJ0FC0WEFJ-E2
U5: PIC16F1826-ISO

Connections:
+5V: F2.2, J1.4, J2.4
+10V: C2.1, C6.2, C8.2, C10.2, J4.3, J5.3, J6.1, J7.1, J8.1, R2.1, U1.8, U2.8, U3.8, U4.1
+12V: F1.2, J1.5, J2.5
/DIP_1: R5.2, SW1.8, U5.2
/DIP_2: R6.2, SW1.7, U5.3
/DIP_3: R7.2, SW1.6, U5.16
/DIP_4: R10.2, SW1.5, U5.15
/ICSPCLK: J3.1, U5.12
/ICSPDAT: J3.2, U5.13
/P1_IN: J4.1, R8.2
/P2_IN: J5.1, R9.2
/PRESSURE_1: C4.1, R8.1, U5.8
/PRESSURE_2: C5.1, R9.1, U5.9
/SCL: J1.2, J2.2, TP4.1, U5.10
/SDA: J1.1, J2.1, TP5.1, U5.7
/STRAIN_OUT_1: C7.1, R13.1, TP1.1, U5.17
/STRAIN_OUT_2: C9.1, R16.1, TP2.1, U5.18
/STRAIN_OUT_3: C11.1, R19.1, TP3.1, U5.1
/~MCLR: J3.5, R1.2, U5.4
GND: C1.2, C2.2, C3.1, C4.2, C5.2, C6.1, C7.2, C8.1, C9.2, C10.1, C11.2, D2.2, D3.2, D4.2, J1.3, J2.3, J3.3, J4.2, J5.2, J6.4, J7.4, J8.4, R3.2, R4.2, R12.1, R15.1, R18.1, SW1.1, SW1.2, SW1.3, SW1.4, U1.5, U2.5, U3.5, U4.3, U4.EPAD, U5.5
unnamed: C1.1, F1.1, U4.8
unnamed: D1.1, R4.1
unnamed: D1.2, U5.11
unnamed: D2.1, R13.2, U1.7
unnamed: D3.1, R16.2, U2.7
unnamed: D4.1, R19.2, U3.7
unnamed: J6.2, U1.1
unnamed: J6.3, U1.4
unnamed: J7.2, U2.1
unnamed: J7.3, U2.4
unnamed: J8.2, U3.1
unnamed: J8.3, U3.4
unnamed: R2.2, R3.1, U5.6
unnamed: R11.1, U1.3
unnamed: R11.2, U1.2
unnamed: R12.2, U1.6
unnamed: R14.1, U2.3
unnamed: R14.2, U2.2
unnamed: R15.2, U2.6
unnamed: R17.1, U3.3
unnamed: R17.2, U3.2
unnamed: R18.2, U3.6
VDD: C3.2, F2.1, J3.4, R1.1, R5.1, R6.1, R7.1, R10.1, TP6.1, U4.5, U5.14

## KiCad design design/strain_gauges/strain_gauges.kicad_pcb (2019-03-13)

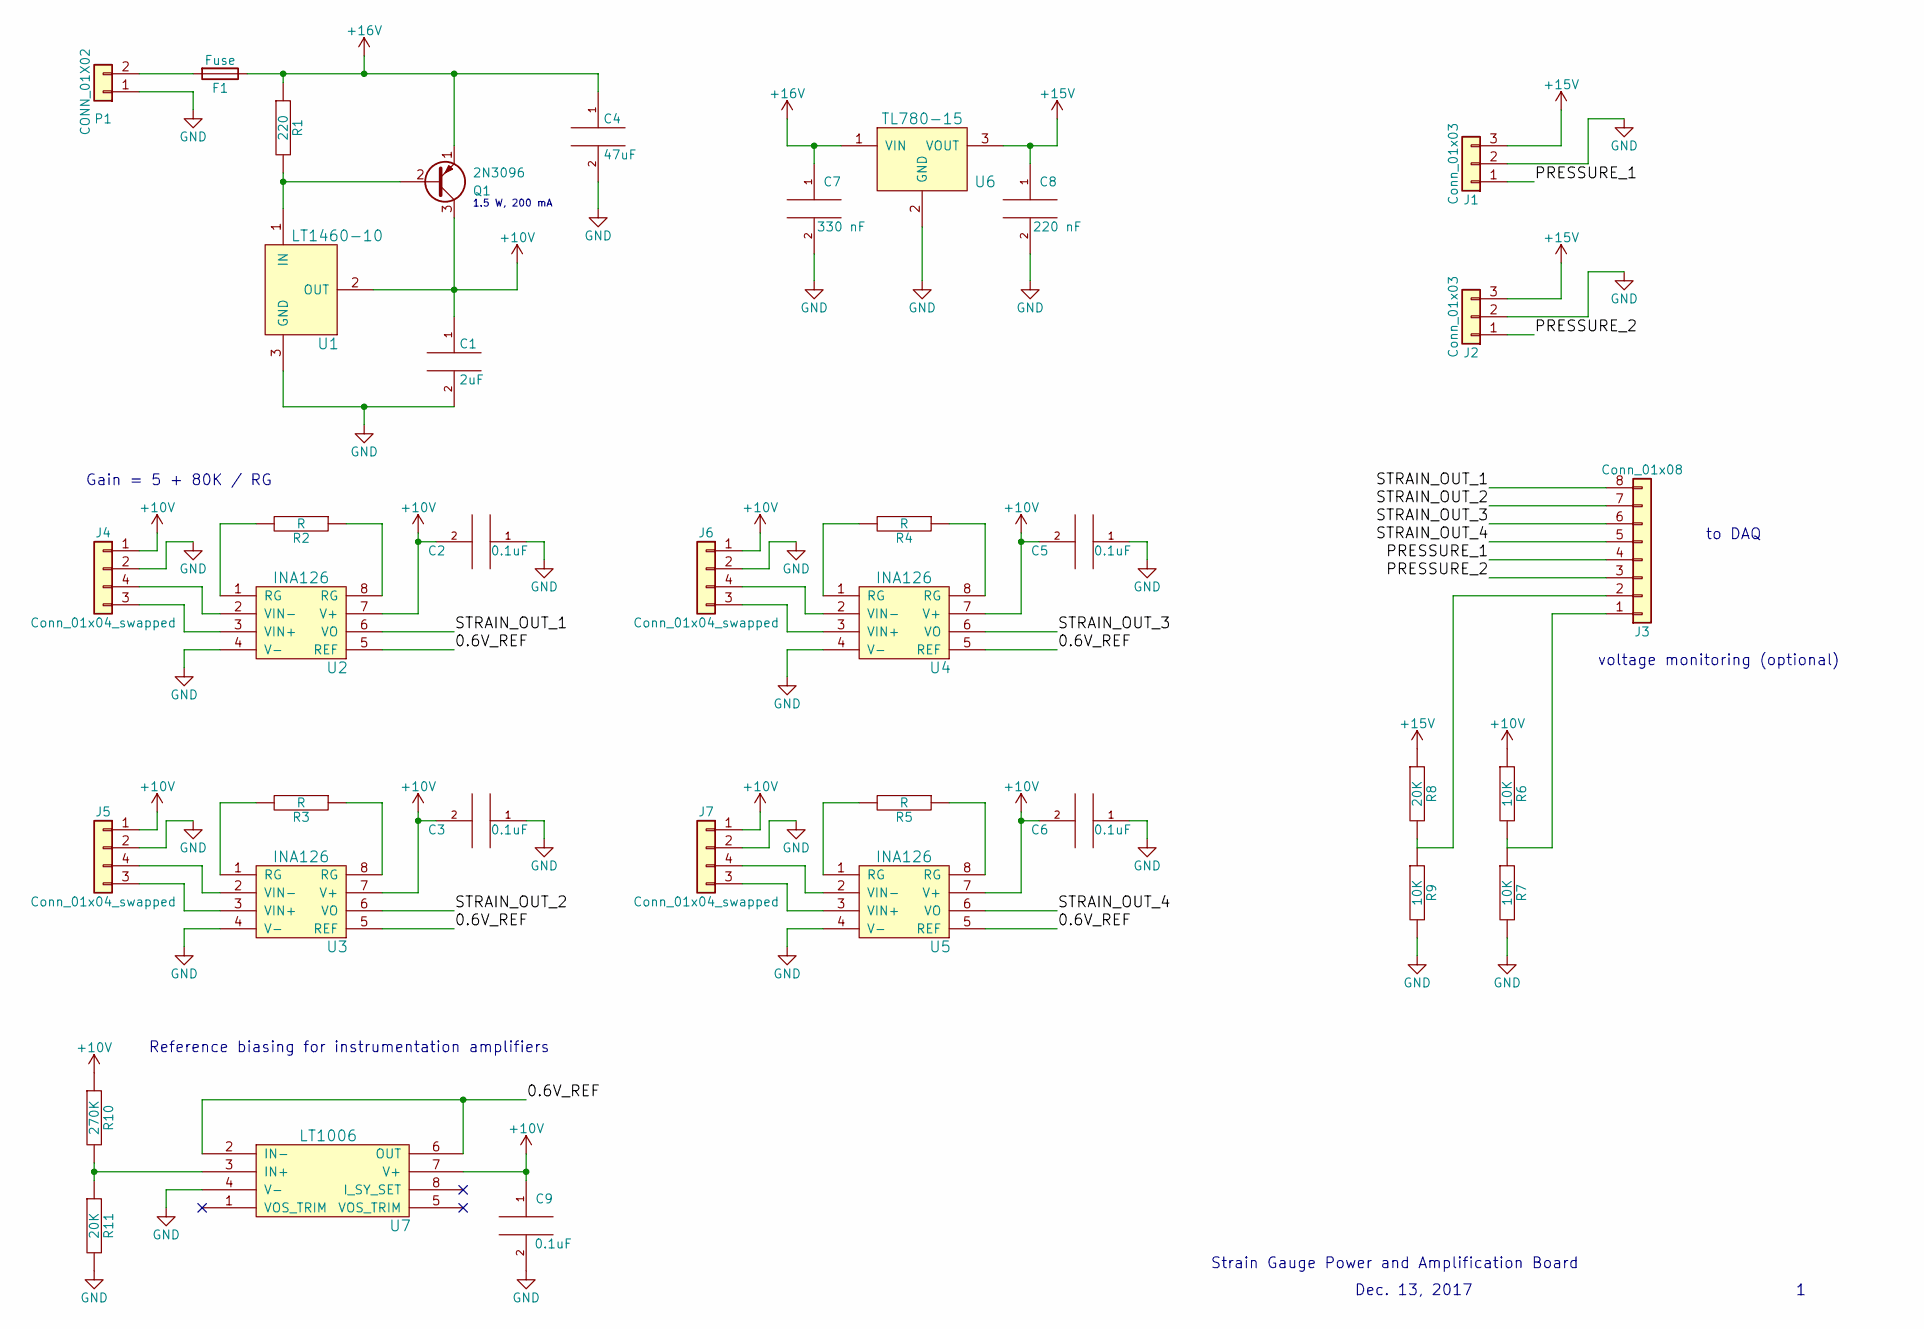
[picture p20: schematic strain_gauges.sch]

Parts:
C1: 2uF; CP_Radial_Tantal_D5.0mm_P2.50mm
C2, C3, C5, C6, C9: 0.1uF; C_0805_HandSoldering
C4: 47uF; CP_Radial_Tantal_D6.0mm_P2.50mm
C7: 330 nF; C_0805_HandSoldering
C8: 220 nF; C_0805_HandSoldering
F1: Fuse; Fuse_1206_3216Metric_Pad1.24x1.80mm_HandSolder
J1, J2: Conn_01x03; PhoenixContact_MCV-G_03x3.50mm_Vertical
J3: Conn_01x08; PhoenixContact_MCV-G_08x3.50mm_Vertical
J4, J5, J6, J7: Conn_01x04_swapped; PhoenixContact_MCV-G_04x3.50mm_Vertical
P1: CONN_01X02; PhoenixContact_MCV-G_02x3.50mm_Vertical
Q1: 2N3096; TO-92_Inline_Narrow_Oval
R1: 220; R_0805_HandSoldering
R2, R3, R4, R5: R; R_0805_HandSoldering
R6, R7, R9: 10K; R_0805_HandSoldering
R8, R11: 20K; R_0805_HandSoldering
R10: 270K; R_0805_HandSoldering
U1: LT1460-10; TO-92_Inline_Narrow_Oval
U2, U3, U4, U5: INA126; DIP-8_W7.62mm
U6: TL780-15; TO-220-3_Vertical
U7: LT1006; DIP-8_W7.62mm

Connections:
+10V: C1.1, C2.2, C3.2, C5.2, C6.2, C9.1, J4.1, J5.1, J6.1, J7.1, Q1.3 (C), R6.1, R10.1, U1.2 (OUT), U2.7 (V+), U3.7 (V+), U4.7 (V+), U5.7 (V+), U7.7 (V+)
+15V: C8.1, J1.3, J2.3, R8.1, U6.3 (VOUT)
+16V: C4.1, C7.1, F1.1, Q1.1 (E), R1.1, U6.1 (VIN)
/0.6V_REF: U2.5 (REF), U3.5 (REF), U4.5 (REF), U5.5 (REF), U7.2 (IN-), U7.6 (OUT)
/PRESSURE_1: J1.1, J3.4
/PRESSURE_2: J2.1, J3.3
/STRAIN_OUT_1: J3.8, U2.6 (VO)
/STRAIN_OUT_2: J3.7, U3.6 (VO)
/STRAIN_OUT_3: J3.6, U4.6 (VO)
/STRAIN_OUT_4: J3.5, U5.6 (VO)
GND: C1.2, C2.1, C3.1, C4.2, C5.1, C6.1, C7.2, C8.2, C9.2, J1.2, J2.2, J4.2, J5.2, J6.2, J7.2, P1.1, R7.2, R9.2, R11.2, U1.3 (GND), U2.4 (V-), U3.4 (V-), U4.4 (V-), U5.4 (V-), U6.2 (GND), U7.4 (V-)
unnamed: F1.2, P1.2
unnamed: J3.1, R6.2, R7.1
unnamed: J3.2, R8.2, R9.1
unnamed: J4.3, U2.3 (VIN+)
unnamed: J4.4, U2.2 (VIN-)
unnamed: J5.3, U3.3 (VIN+)
unnamed: J5.4, U3.2 (VIN-)
unnamed: J6.3, U4.3 (VIN+)
unnamed: J6.4, U4.2 (VIN-)
unnamed: J7.3, U5.3 (VIN+)
unnamed: J7.4, U5.2 (VIN-)
unnamed: Q1.2 (B), R1.2, U1.1 (IN)
unnamed: R2.1, U2.8 (RG)
unnamed: R2.2, U2.1 (RG)
unnamed: R3.1, U3.8 (RG)
unnamed: R3.2, U3.1 (RG)
unnamed: R4.1, U4.8 (RG)
unnamed: R4.2, U4.1 (RG)
unnamed: R5.1, U5.8 (RG)
unnamed: R5.2, U5.1 (RG)
unnamed: R10.2, R11.1, U7.3 (IN+)

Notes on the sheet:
Strain Gauge Power and Amplification Board
Dec. 13, 2017
Gain = 5 + 80K / RG
to DAQ
voltage monitoring (optional)
1.5 W, 200 mA
Reference biasing for instrumentation amplifiers

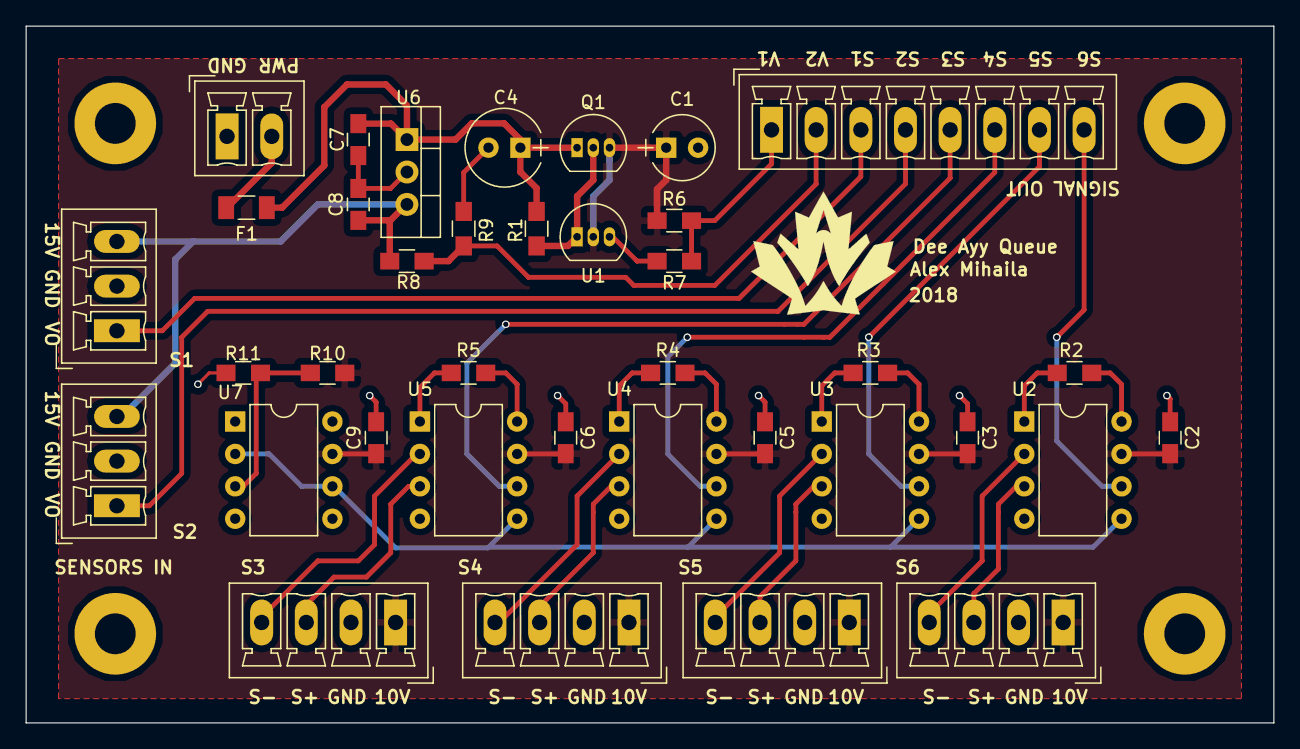
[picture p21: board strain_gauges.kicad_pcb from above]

Board: 2 copper layers, 97.8 x 54.6 mm, 37 parts (0 on the bottom side), 32 nets.

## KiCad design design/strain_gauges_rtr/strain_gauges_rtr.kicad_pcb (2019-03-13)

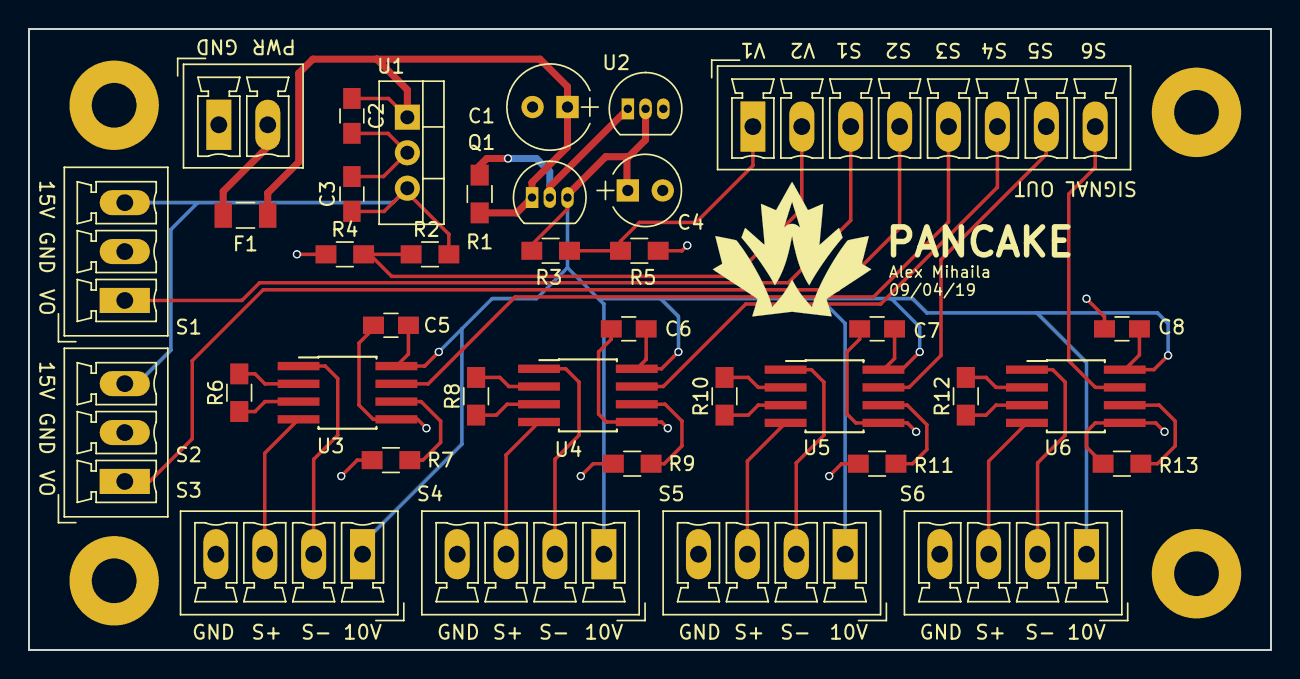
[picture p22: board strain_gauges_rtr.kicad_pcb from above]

Board: 2 copper layers, 88.9 x 44.5 mm, 37 parts (0 on the bottom side), 34 nets.

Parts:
C1: 47uF; CP_Radial_Tantal_D6.0mm_P2.50mm
C2: 330 nF; C_0805_HandSoldering
C3: 220 nF; C_0805_HandSoldering
C4: 2uF; CP_Radial_Tantal_D5.0mm_P2.50mm
C5, C6, C7, C8: 0.1uF; C_0805_HandSoldering
F1: Fuse; Fuse_1206_3216Metric_Pad1.24x1.80mm_HandSolder
J1, J2: Conn_01x03; PhoenixContact_MCV-G_03x3.50mm_Vertical
J3: Conn_01x08; PhoenixContact_MCV-G_08x3.50mm_Vertical
J4, J5, J6, J7: Conn_01x04; PhoenixContact_MCV-G_04x3.50mm_Vertical
P1: CONN_01X02; PhoenixContact_MCV-G_02x3.50mm_Vertical
Q1: 2N3096; TO-92_Inline_Narrow_Oval
R1: 220; R_0805_HandSoldering
R2: 20K; R_0805_HandSoldering
R3, R4, R5: 10K; R_0805_HandSoldering
R6, R8, R10, R12: R; R_0805_HandSoldering
R7, R9, R11, R13: 0; R_0805_HandSoldering
U1: TL780-15; TO-220-3_Vertical
U2: LT1460-10; TO-92_Inline_Narrow_Oval
U3, U4, U5, U6: INA826; SOIC-8_3.9x4.9mm_Pitch1.27mm_HandSoldering

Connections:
+10V: C4.1, C5.2, C6.2, C7.2, C8.2, J4.1, J5.1, J6.1, J7.1, Q1.3, R3.1, U2.2, U3.8, U4.8, U5.8, U6.8
+15V: C3.1, J1.3, J2.3, R2.1, U1.3
+16V: C1.1, C2.1, F1.1, Q1.1, R1.1, U1.1
/PRESSURE_1: J1.1, J3.3
/PRESSURE_2: J2.1, J3.4
/STRAIN_OUT_1: J3.5, U3.7
/STRAIN_OUT_2: J3.6, U4.7
/STRAIN_OUT_3: J3.7, U5.7
/STRAIN_OUT_4: J3.8, U6.7
GND: C1.2, C2.2, C3.2, C4.2, C5.1, C6.1, C7.1, C8.1, J1.2, J2.2, J4.4, J5.4, J6.4, J7.4, P1.1, R4.2, R5.2, R7.1, R9.1, R11.1, R13.1, U1.2, U2.3, U3.5, U4.5, U5.5, U6.5
unnamed: F1.2, P1.2
unnamed: J3.1, R3.2, R5.1
unnamed: J3.2, R2.2, R4.1
unnamed: J4.2, U3.1
unnamed: J4.3, U3.4
unnamed: J5.2, U4.1
unnamed: J5.3, U4.4
unnamed: J6.2, U5.1
unnamed: J6.3, U5.4
unnamed: J7.2, U6.1
unnamed: J7.3, U6.4
unnamed: Q1.2, R1.2, U2.1
unnamed: R6.1, U3.3
unnamed: R6.2, U3.2
unnamed: R7.2, U3.6
unnamed: R8.1, U4.3
unnamed: R8.2, U4.2
unnamed: R9.2, U4.6
unnamed: R10.1, U5.3
unnamed: R10.2, U5.2
unnamed: R11.2, U5.6
unnamed: R12.1, U6.3
unnamed: R12.2, U6.2
unnamed: R13.2, U6.6

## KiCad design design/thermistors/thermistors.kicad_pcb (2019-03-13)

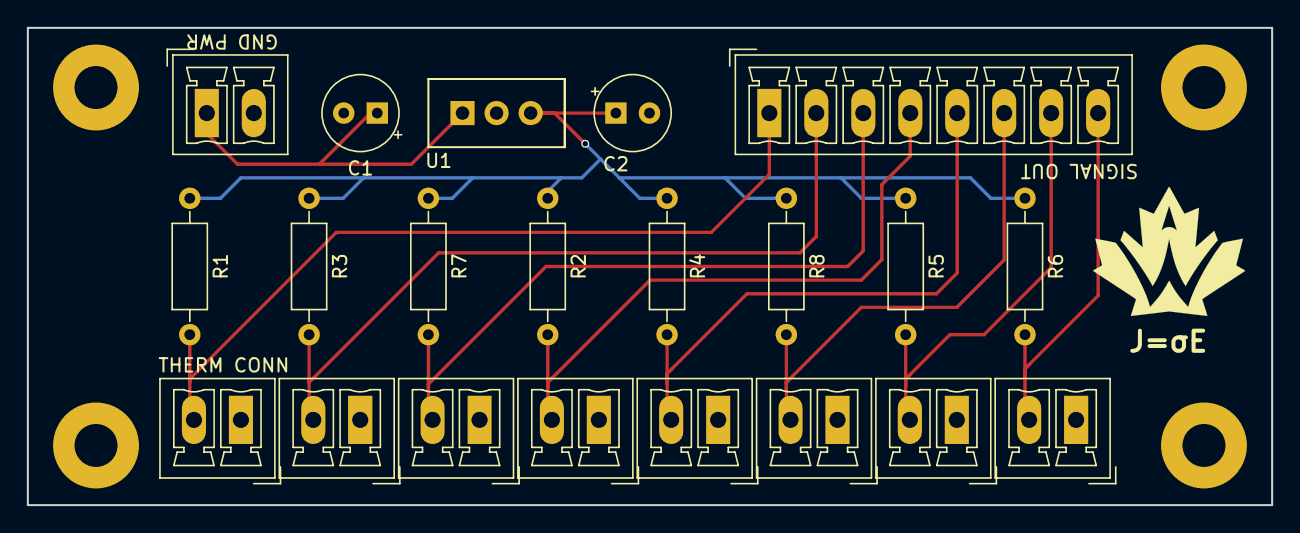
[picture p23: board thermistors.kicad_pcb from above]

Board: 2 copper layers, 92.7 x 35.6 mm, 21 parts (0 on the bottom side), 11 nets.

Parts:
C1, C2: 10uF; CP_Radial_Tantal_D5.5mm_P2.50mm
J1, J3, J4, J5, J6, J7, J8, J9, J10: Conn_01x02; PhoenixContact_MCV-G_02x3.50mm_Vertical
J2: Conn_01x08; PhoenixContact_MCV-G_08x3.50mm_Vertical
R1, R2, R3, R4, R5, R6, R7, R8: R; R_Axial_DIN0207_L6.3mm_D2.5mm_P10.16mm_Horizontal
U1: R-78E; R-78-converter

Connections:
+5V: C2.1, R1.1, R2.1, R3.1, R4.1, R5.1, R6.1, R7.1, R8.1, U1.3
/16V: C1.1, J1.1, U1.1
/therm_1: J2.1, J3.2, R1.2
/therm_2: J2.2, J5.2, R3.2
/therm_3: J2.3, J9.2, R7.2
/therm_4: J2.4, J4.2, R2.2
/therm_5: J2.5, J6.2, R4.2
/therm_6: J2.6, J10.2, R8.2
/therm_7: J2.7, J7.2, R5.2
/therm_8: J2.8, J8.2, R6.2
GND: C1.2, C2.2, J1.2, J3.1, J4.1, J5.1, J6.1, J7.1, J8.1, J9.1, J10.1, U1.2

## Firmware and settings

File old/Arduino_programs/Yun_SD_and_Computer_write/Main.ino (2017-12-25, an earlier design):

#include "Arduino.h"

#include "sensorData.h"
#include "thermistor.h"

#define DECIMALS 3	// we have a precision of ~3 mV so no point in adding more decimal places
#define NUM_SENSORS 6
#define NUM_THERMISTORS 4
int ledPin =  13; 

void setup() {
  // initialize serial communication at 9600 bits per second:
  Serial1.begin(57600);//for Yun, serial 1 prints to SD card
  Serial.begin(57600);//for Yun, serial prints to USB port
}


void loop() {
  // make a string that start with a timestamp for assembling the data to log:

  long timing;
  SensorData sensorData[6];
  thermistor Thermistor[4];

  sensorData[0].setParams("100_lb", A0, 25.0, -12.734);
  sensorData[1].setParams("P1", A1, 610.55, 46.965);
  sensorData[2].setParams("P2", A4, 603.97, -231);

  sensorData[3].setParams("SP1", A3, 602.02, -68.644);
  sensorData[4].setParams("SP2", A2, 595.01, -61.697);
  sensorData[5].setParams("2000_lb", A5, 746.446, -73.8);

  Thermistor[0].setParams("Red_T1", A8, 3600, 800);
  Thermistor[1].setParams("Blue_T2", A9, 3600, 800);
  Thermistor[2].setParams("White_T3", A10, 3600, 800);
  Thermistor[3].setParams("Green_T4", A11, 3600, 800);

  for (int i = 0; i < NUM_SENSORS; ++i) {
    pinMode(sensorData[i].pin_, INPUT);
  }
  pinMode(Thermistor[0].pin_,INPUT);
  pinMode(ledPin, OUTPUT);

  Serial1.print("\n\n\n");
  Serial.print("\n\n\n");
  Serial1.print("Time ");
  Serial.print("Time ");
  for (int i = 0; i < NUM_SENSORS; ++i) {
   Serial1.print(sensorData[i].name_);
   Serial1.print(" ");
   Serial.println(sensorData[i].name_);
   Serial.println(" ");
  }
  Serial1.print(Thermistor[0].name_);
  Serial1.print(" ");
  Serial.print(Thermistor[0].name_);
  Serial.print(" ");
  
  
  Serial1.print("\n");
  Serial.print("\n");

  while (true) {

while((micros()<(timing+19996))&&(micros()>timing))
{}
timing=micros();
    for (int i = 0; i < NUM_SENSORS; ++i) {
      sensorData[i].readToArray();
    }
     Thermistor[0].readToArray();
    Serial1.print(micros());
    Serial1.print(", ");
    Serial.print(micros());
    Serial.print(", ");

    for (int i = 0; i < NUM_SENSORS; ++i) {
      Serial1.print(sensorData[i].voltageAvg(), DECIMALS);
      Serial1.print(" ");
      Serial.print(sensorData[i].voltageAvg(), DECIMALS);
      Serial.print(" ");
    }
    for (int i = 0; i < NUM_THERMISTORS; ++i) {
    Serial1.print(Thermistor[i].convertedVal(), DECIMALS);
    Serial1.print(" ");
    Serial.print(Thermistor[i].convertedVal(), DECIMALS);
    Serial.print(" ");
    }
    Serial.print("\n");
    Serial1.print("\n");
  }
  
  while (1){     //Blink the Status LED because we're done!
  digitalWrite(ledPin, HIGH);
  delay(100);
  digitalWrite(ledPin, LOW);
  delay(1000); }
  
}

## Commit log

2017-12-23 Initial commit
    Add old schematics, datasheets, and strain gauge
    circuit preliminary design.
    [DAQrev2_clean.sch, strain_gauges.kicad_pcb, strain_gauges.sch]
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2018-01-02 Fix voltage monitoring, add gitignore
    [strain_gauges.sch]
2018-01-03 Fix strain gauge schematic
    - swap out pnp transistor for a higher power one
    - misc rearrangments
    [strain_gauges.sch]
2018-01-04 Preliminary board layout (no tracks)
    [strain_gauges.kicad_pcb, strain_gauges.sch]
2018-01-04 Revised board layout
    - move screw terminal locations
    - power op amps from 10V line
    - misc connector numbering switches
    [strain_gauges.kicad_pcb, strain_gauges.sch]
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2018-01-05 First pass board routing
    - will probably go back and change placement of power blocks
    - likely not final
    [strain_gauges.kicad_pcb, strain_gauges.sch]
2018-01-06 Board layout & routing rework
    - Move the power blocks further into the board
    - ground planing not done yet
    [strain_gauges.kicad_pcb, strain_gauges.sch]
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2018-01-06 Make power traces fatter
    [strain_gauges.kicad_pcb]
2018-01-11 Correct PNP orientation in schematic
    Also swap out the part for one I have on hand (2N3906)
    [strain_gauges.kicad_pcb, strain_gauges.sch]
2018-01-12 Finish PCB
    - add ground plane
    - add silk screening
    - still open for review on PCB design
    [strain_gauges.kicad_pcb]
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2018-01-15 minor routing & silk screen changes
    [strain_gauges.kicad_pcb]
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2018-02-27 Add old strain gauge fabrication files
    Note: will be replaced when new board is printed. Kept here for backup
    only.
    [strain_gauges-Edge.Cuts.gm1, strain_gauges.drl, strain_gauges.gbl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]
2018-03-02 Fix INA126 reference biasing (sch)
    [strain_gauges.sch]
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2018-04-09 Circuit and layout for INA826 variant
    Add new strain gauge circuitry based on the INA826. This PCB should be
    sent to fab at the same time as the INA126 bias corrected one. Using
    this board would be preferred since the 826 is a proper rail to rail
    instrumentation amplifier, but the other one is fine if this one has
    problems. The INA826 is available in SMD packages only and deadbugs +
    breadboard tests aren't really feasible.
    Work done so far: schematic and PCB layout, no routing.
    [instr_amp.sch, strain_gauges.kicad_pcb, strain_gauges.sch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]
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2019-03-13 Add schematics and pcb files for thermistor board
    [thermistor_divider-2018-10-27-14-53-50.sch, thermistors-2018-10-27-14-53-50.sch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]
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2019-03-13 Add most up to date rtr strain gauge files
    [instr_amp-2018-10-03-15-05-33.sch, instr_amp-2018-10-03-15-06-41.sch, strain_gauges_rtr-2018-10-03-15-06-41.sch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]
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2020-03-03 Update calibration and graphs
    Fix the names of the graphs and calibation values updated to latest test
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2020-03-21 Fix some suggestions
    [i2c_pancake.sch, instr_amp.sch]
2020-04-29 Finish adressing Alex and Jared's comments with the exception of issue with high drop out voltage on current amp.
    [i2c_pancake.sch, instr_amp.sch]
2020-04-29 Replace internal DC power supply with a Low-Dropout Regulator
    The LDO regulator will convert the 12 volt input from the LiPo battery to a stable 10 volt
    internal supply.
    [i2c_pancake.sch, instr_amp.sch]
2020-05-10 Update component footprints to prepare for PCB Layout update
    The footprints of many components in the I2C Pancake Board
    design have been updated to prepare for a new PCB Layout.
    [i2c_pancake.sch, instr_amp.sch]
2020-06-01 Add footprints to all schematic symbols
    All schematic symbols have been assigned footprints.
    PCB dimensions have been set, and most of the components have
    been placed.
    [i2c_pancake.kicad_pcb, i2c_pancake.sch, instr_amp.sch]
2020-06-01 Finish the preliminary PCB layout
    The preliminary PCB layout is finished. However, there is
    room for improvement. The PCB layout should be reviewed and
    polished before continuing with routing.
    [i2c_pancake.kicad_pcb]
2020-06-14 Improve Layout of Passive Components on the Pancake Board
    -Fuse has been replaced with a 1206 polyfuse
    -passive components have been rearranged in a more logical manner
    -DRC rules have been imported from the RLCS v2 project
    [i2c_pancake.kicad_pcb, i2c_pancake.sch, instr_amp.sch]
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2020-07-05 Fix some bad routing and silkscreen placement
    [i2c_pancake.kicad_pcb]
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2020-07-12 Revert "Add pinout labels to connectors"
    This reverts commit 21ee90c71cbcb3ee9da454b06d43e90a118cf2fc.
    Discard initial routing for the I2C Pancake board.
    The routing will be done in a future commit with 4 copper layers.
    [i2c_pancake.kicad_pcb, i2c_pancake.sch, instr_amp.sch]
2020-07-12 Remove unecessary KiCAD files.
    The .gitignore has been updated to ignore KiCAD backup and cache files.
    [instr_amp-2018-10-03-15-05-33.sch, instr_amp-2018-10-03-15-06-41.sch, strain_gauges_rtr-2018-10-03-15-06-41.sch]
2020-07-13 Revert "Add pinout labels to connectors"
    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
    [i2c_pancake.kicad_pcb]
2020-07-13 Fix corrupted PCB file
    [i2c_pancake.kicad_pcb]
2020-07-20 Modify the board settings to have four layers.
    Pinout labels have been moved to the top of the board.
    [i2c_pancake.kicad_pcb]
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2020-07-20 Create initial 4-layer routing for I2C Pancake Board.
    This is my first attempt at doing 4-layer routing. There are
    some outstanding issues with the routing here. Namely, the
    coupling/decoupling capacitors have rather long traces
    connecting them to their respective devices. These issues
    will be fixed in future commits.
    [i2c_pancake.kicad_pcb, i2c_pancake.sch, instr_amp.sch]
2020-07-20 Improve board routing.
    Coupling/decoupling capacitors are now closely connected to their
    respective devices.
    [i2c_pancake.kicad_pcb]
2020-08-23 Increase I2C line clearance to 20 mils.
    This will minimize cross-talk with I2C lines.
    [i2c_pancake.kicad_pcb, i2c_pancake.sch]
2020-08-23 Replace fuse footprint with standard 0805 SMD footprint.
    A note has been added to the schematic regarding expected current
    and trip current through the fuse.
    [i2c_pancake.kicad_pcb, i2c_pancake.sch, instr_amp.sch]
2020-08-23 Add test points to the Pancake board.
    Test points were added to the outputs of each strain guage amp.
    [i2c_pancake.kicad_pcb, i2c_pancake.sch, instr_amp.sch]
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2020-09-23 Replace +5V and +12V routing with 12 traces
    [i2c_pancake.kicad_pcb]
2020-09-23 Finish I2C Pancake board design and add gerbers!
    [i2c_pancake-B_Cu.gbl, i2c_pancake-B_Mask.gbs, i2c_pancake-B_Paste.gbp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]
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2020-09-28 Implement improvements suggested by Zachariah Mears and update Gerbers
    [i2c_pancake-B_Cu.gbl, i2c_pancake-B_Mask.gbs, i2c_pancake-B_Paste.gbp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]
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2020-10-03 Replace linear regulator to match the recent Digikey order
    [i2c_pancake.kicad_pcb, i2c_pancake.sch, instr_amp.sch]
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2020-10-10 Add RC filters to the analog inputs of the PIC
    This commit also includes a new and improved routing.
    [i2c_pancake-B_Cu.gbl, i2c_pancake-B_Mask.gbs, i2c_pancake-B_Paste.gbp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]
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2020-10-11 Repair broken and missing library references
    [i2c_pancake.kicad_pcb, i2c_pancake.sch, instr_amp.sch]
2020-10-11 Rename "I2C Pancake" to "I2C_Pancake" and update gerbers
    [i2c_pancake-B_Cu.gbl, i2c_pancake-B_Mask.gbs, i2c_pancake-B_Paste.gbp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]
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2020-10-15 Fix routing for +5V trace
    [i2c_pancake-B_Cu.gbl, i2c_pancake-B_Mask.gbs, i2c_pancake-B_Paste.gbp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]
2020-10-15 Repair broken library references
    [i2c_pancake.sch, instr_amp.sch]
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2021-05-22 Create initial commit for SPI temp sensing board
    [spidey_sense.kicad_pcb, spidey_sense.sch]
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2021-09-12 Just regulate one voltage per board, remove accuracy compensation
    [buck_fb.sch, ldo.sch, power_board.sch]
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2021-10-04 Changed some capacitors based on the LDO's application note / suggested layout, layout done
    [buck_fb.sch, ldo.sch, power_board.kicad_pcb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]
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2021-10-19 Fix inconsistent silkscreen positions
    [power_board.kicad_pcb]
2021-10-20 Oh yes the silkscreen is a thing that exists
    [power_board.kicad_pcb]
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2021-12-21 Tweak value of C3, replace U1 with the part we ordered
    [buck_fb.sch]
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2022-01-27 Added vias to avoid GND loops
    [Amplifier.kicad_sch, spidey_sense.kicad_pcb, spidey_sense.kicad_sch]
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2022-10-24 Changed pin header orientations and added silkscreen labels
    [spidey_sense.kicad_pcb]
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2024-03-15 Daq patch panel (#21)
    * Create DaqPatchPanel.txt
    * Create Daq_Patch_Panel.txt
    * First Schematic Editing
    Basic Sensor layout for 1 sensor
    * Changes to delete switches and duplicate board setup
    * Added Jumpers
    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
    [DAQ_Patch_Panel.kicad_pcb, DAQ_Patch_Panel.kicad_sch, sensor_comp.kicad_sch]
2024-03-15 Daq power board (#22)
    * Create power_board2
    * Add files via upload
    * Add files via upload
    * Delete design/power_board2
    * Create keep
    * Update and rename design/buck_converter_new.kicad_sch to design/power_board_2/buck_converter_new.kicad_sch
    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
    [buck.kicad_sch, buck_fb.sch, buck_fixed.sch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]
2024-03-15 Thermocouple board (#23)
    * Removed old spidey sense files and added new thermocouple board schematic
    * Deleted remaining spidey sense files
    * Renamed SDI tag to SDO
    * Added optional can termination resistor
    * Addressed Artem's comments
    * Addressed comments added 3.3V PIC
    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
    [Amplifier.kicad_sch, spidey_sense.kicad_pcb, spidey_sense.kicad_sch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]

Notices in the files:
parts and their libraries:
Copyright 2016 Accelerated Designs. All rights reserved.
